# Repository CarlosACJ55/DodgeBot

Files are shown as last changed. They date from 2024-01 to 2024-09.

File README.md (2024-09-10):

# DodgeBot

<!-- [![Python application](https://github.com/CarlosACJ55/DodgeBot/actions/workflows/python-app.yml/badge.svg)](https://github.com/CarlosACJ55/DodgeBot/actions/workflows/python-app.yml) -->
## Youtube Demo Video Links
Dodgebot Purdue Boxing Club Review (https://youtube.com/watch?v=Q3NQfAVkUB4)

Dodgebot Demo 1 (https://www.youtube.com/shorts/NQUYcLnN8nE)
Dodgebot Demo 2 (https://youtube.com/shorts/Dirlxg9N7j0)

## Description

Punch-dodging robot project started as a senior design group project for ECE 47700 group 5 at Purdue University.

<!-- ### Project Website

Learn about PunchBot on our Project Website!
Https://engineering.purdue.edu/477grp5/ -->

### Dependencies

* Brains coded in Python 3
  - Packaged with **Poetry**
  - Developped with **Pytest**
  - Ui designed in **tkinter**
* Braum controlled by **STM32F7** programmed in **C**
  - Generated drivers with **STM32CubeMX**
  - Depelopped for **Yaskawa** **SGM7G-30A** & **SGM7G-20A** motors

## Authors

* Yusuf Jarada
* Maximillian Drach
* Ayman Motoda
* Carlos Cotera

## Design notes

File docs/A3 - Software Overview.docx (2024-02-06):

# Software Overview

# Year: 2024 Semester: Fall Team: 5 Project: PunchBot

# Creation Date: 01/23/2024 Last Modified: January 27, 2024

# Author: Carlos Cotera Email: ccoteraj@purdue.edu

# 1.0 Software Overview

PunchBot has a couple main requirements for success. From the perspective of a user, here is how the interactions are expected to go, as well as a highlight of where the key software is implemented:

After turning on the device, the user should be able to stand in view of the cameras, within arm’s reach, then a second user should be able to initialize punch detection mode1. At this point, the cameras continually analyze the movement of the player’s gloves and once the start of a punch is detected by the tracking script, we can now trigger the trajectory prediction algorithm2. Here, after quickly estimating the general direction of the punch, the robot should be able to determine an optimal dodging direction. Then, the STM and jetson chips use UART via EtherCAT to give the motors SPI commands3. The first motor is responsible for orienting PunchBot circularly to face a direction, while the second motor is meant to rapidly tilt the target forward to perform a dodge that imitates a real-life boxer by pivoting at an approximation of the hips.

At this point, the punch is completed and the bot will have to re-calculate how to return to its starting point as fast as possible, during the return, we expect that it would be best to continue in punch detection mode, so the bot is ready to interrupt itself and make another dodge, but this might prove to be either unnecessary given the final speed or too complex for the hardware, so we can still determine this later. Once back in punch detection mode we want the main script to cycle between these modes efficiently until the bot is deactivated via user input.

As a potential advancement, we could complete a game design for the project as described in the flowchart in the appendix 1 below, the main machine state functionality that we need to achieve is in appendix 2.

2.0 Description of Algorithms

Utilizing the OpenCV library, NumPy, and PyTorch for computer vision. The real-time video processing from a camera feed is done as follows, following the KMeans clustering approach to analyze motion via the kmeans PyTorch import:

Initializing

frame_resize: Resizes a video frame.

calibration_circle: Adds a calibration circle to the frame.

K-Means Clustering Functions:

kmeans_gpu: Applies K-Means clustering to identify objects in the video feed and returns their coordinates and cluster centers.

Initialize parameters like pixel center, camera height, user height, and camera orientation.

Main Loop:

Continuously captures video frames, converting frames to the HSV color space and applying color filtering to identify objects in the specified color range (yellow gloves). With this processed data, we use K-Means clustering to identify the objects' pixel coordinates and cluster centers. We can also track the movement of the identified objects and calculate avoidance maneuvers for a simulated robot.

# 3.0 Description of Data Structures

# Based on our mode functions, there would also be a need of data structures for motion tracking and motion analyzing. One of the key data structures we are taking advantage of for the PunchBot is a displacement vector for the following uses (examples from current testing script):

img_2_vector and vector_2_image: Convert image to vector and vice versa.

pixel_2_cords and cords_2_pixel: Convert pixel coordinates to real-world coordinates and vice versa.

To track the motion of user, we would need to set data points from the image of the user using camera. Inside this data structure, it will capture and tracks each data points of the user’s glove motion. By comparing x, y, z values, we can detect the punch because user will move their arms forward. In analyzing motion structure, it will calculate possible pathway of the punch based on the data point. I the main loop, punch detection mode captures frames from the camera, processes them, performs color segmentation, and tracks objects using k-means clustering. The tracked object's position and movement are used for some form of robotic control or object avoidance.

Examples of other key data structures:

lower_bound_gloves = np.array([20, 100, 100])

upper_bound_gloves = np.array([30, 255, 255])

color_mask_gloves = cv.inRange(hsv_frame, lower_bound_gloves, upper_bound_gloves)

Above, we use np arrays to produce a data structure that can perform vector like operations efficiently and with short, readable syntax. As for object Tracking with k-means:

marked_pixel_coords = np.column_stack(np.where(color_mask_gloves > 0)) marked_pixel_coords = torch.tensor(marked_pixel_coords, dtype=torch.float16, device=device) cord_list, punch_pixel_cord_centers = kmeans_gpu(marked_pixel_coords, 2, punch_pixel_cord_centers, num_punches)

This extracts coordinates of colored pixels and performs k-means clustering to identify objects.

The tracked object's centroids are calculated and used for further analysis.

# 4.0 Sources Cited:

E. Ecosystem, “Understanding K-Means clustering in machine learning,” Medium, May 17, 2022. [Online]. Available: https://towardsdatascience.com/understanding-k-means-clustering-in-machine-learning-6a6e67336aa1

# Appendix 1: Program Flowcharts (camera test)

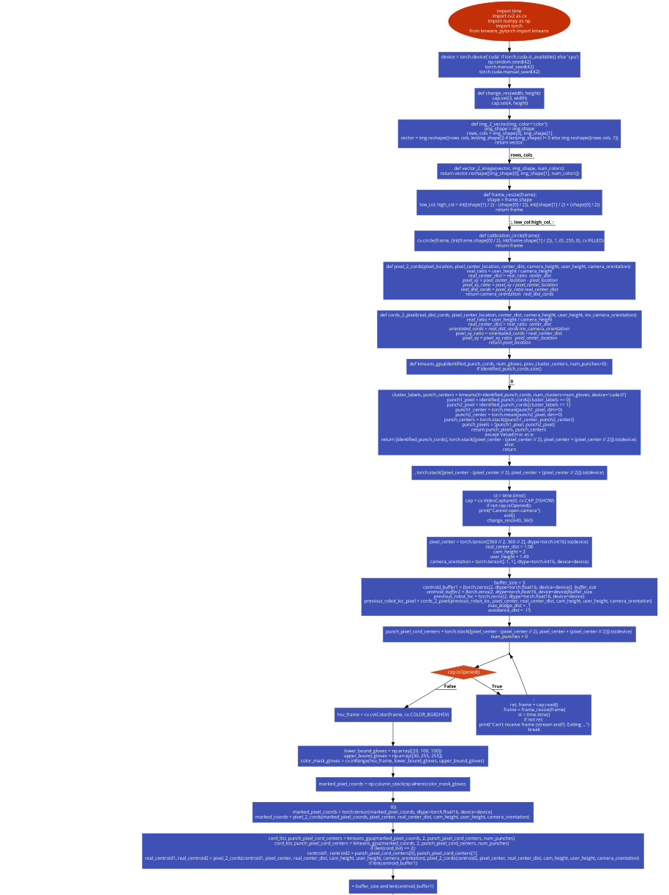
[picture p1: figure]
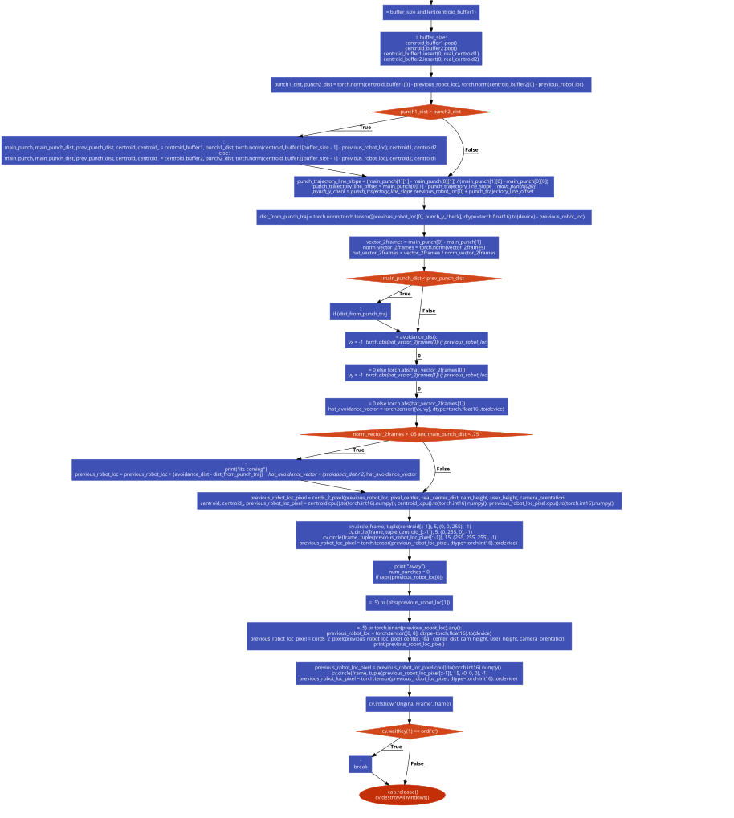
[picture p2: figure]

# Appendix 2: State Machine Diagrams

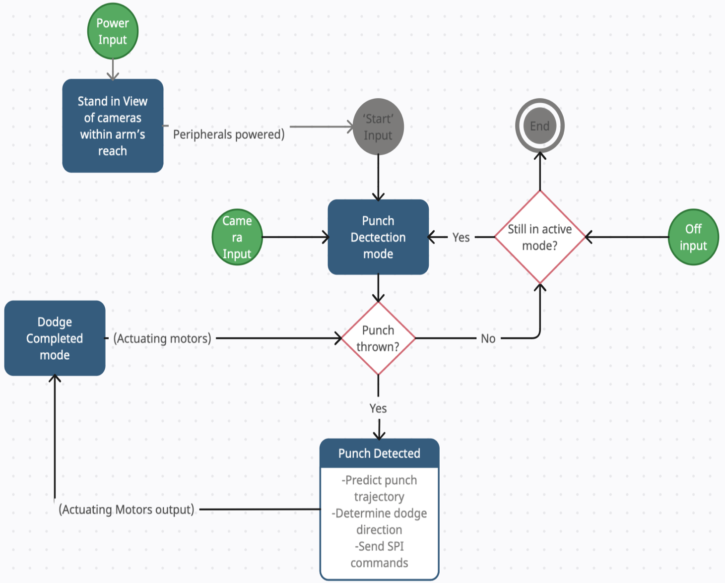
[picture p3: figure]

ECE 477: Digital Systems Senior Design Last Modified: 01-27-2024

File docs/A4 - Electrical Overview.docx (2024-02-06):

# Electrical Overview

# Year: 2024 Semester: Spring Team: 05 Project: Dodgebot

# Creation Date: February 1, 2024 Last Modified: February 1, 2024

# Author: Ayman Motoda Email: aelnamr@purdue.edu

# Assignment Evaluation: See Rubric on Brightspace Assignment

# 1.0 Electrical Overview

For this project, we are using a 32-bit microcontroller to communicate with an external computer to receive motor coordinates from the position calculation performed. We then take this value and feed it to the motor controller. To communicate with the computer, we are going to use UART at the maximum settable baud rate by the setup software to allow low latency between the controller and the computer. To communicate with the motor, we are going to use CANbus since this is the only natively supported communication protocol used by the microcontroller. The maximum baud rate of the motor interface is 1Mbit/s [1], so we are going to communicate with the motor at that rate also for lower latency.

# 2.0 Electrical Considerations

For our power delivery system, our input voltage is going to be at 12V and can be delivered at 5A. The required voltages for the different components around our board are going to be 5V and 3.3V. We will be using buck controllers to create these voltages. The STM32F2 chip that we are using has a typical operating voltage of 3.3V [2]. The NVIDIA Jetson computer that we are using has an operating voltage of 5V [3]. Any peripherals that are connected to both of these computers will be powered off by either of these chips.

The main essence of the operation of our robot is going to be speed. Our target is to dodge a punch that would occur in 100ms. We are going to allocate around 50ms to the computation and signal communication time. This means that having a higher clock speed will help in our baud rate in our communication systems. The maximum baud rate of UART on our STM32 chip is around 1Mbit/s [2]. This requires a clock rate of 16MHz for just the UART lines. The other communication system of CANbus will require the same baud rate and clock speed to run it. This means that at least a operating frequency of >32MHz is required for our system. For reliable operation, we will want to run at a frequency of >100MHz.

The total power that can be supplied to the board through the 12V input is 60W. The total output power that can be supplied by the switching regulators is 5V at 5A or 25W, and 3.3V at 5A or 16.5W[4]. The total power output by the regulators is 41.5W. Since we are using switching regulators that are at least 82% efficient, we only have a total power usage of 51W which is within our input supply power demands.

Device | Max Current Draw [A] (5V) | Device | Max Current Draw [A] (3.3V)
NVIDIA Jetson [3] | 4 | STM32F2 [2] | 0.120

# Table 1: Electrical Max Current Component Requirements

# Any peripherals connected to these devices are within the power draw specifications provided as they are powered off these computers/microcontrollers, so no additional power draw should occur.

# 3.0 Interface Considerations

The two utilized interfaces in this project are UART and CANbus. UART is used for communicating with the main computer. The main computer has the motor commands we need to send to the motor controllers. The STM32 and the Jetson are going to be set up for UART so that we can transmit this data. We chose this methodology because the distance is going to be short between both controllers, so using a synchronous protocol was not a concern since it will require less lines as well as making it much easier to integrate with the Jetson. The baud rate is also very high, so we can get very low latency between both controllers. A 1Mbit baud rate allows transmission times of way below 1ms [2]. The second communication protocol that is being used is CANbus. This is because this is the only way we can communicate with the motor controllers. This has the same baud rate as UART, so there is no bottle neck for each other except for the speed of the microcontroller to take the data and create the new packet frame for the other communication interface [5]. The peripheral interface that we will focus on is USB, which is built into the Jetson, but it is to receive the camera feed.

# 4.0 Sources Cited:

[1] “CAN-Bus Interface connector X13/X14,” Kollmorgen.com, 2023. https://webhelp.kollmorgen.com/akd2g/english/Content/AKD2G-S%20Install/e/AKD2S_install_09_21_00_CANbus%20interface.htm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 (accessed Feb. 01, 2024).

[2] STMicroelectronics, “Arm®-based 32-bit MCU, 150 DMIPs, up to 1 MB Flash/128+4KB RAM, USB OTG HS/FS, Ethernet, 17 TIMs, 3 ADCs, 15 comm. interfaces and camer,” STMicroelectronics STM32F205xx STM32F207xx, Jul. 2020. https://www.st.com/resource/en/datasheet/stm32f207vg.pdf

[3] NVIDIA, “DATA SHEET NVIDIA Jetson Nano System-on-Module Maxwell GPU + ARM Cortex-A57 + 4GB LPDDR4 + 16GB eMMC,” NVIDIA Developer, 2014. https://developer.download.nvidia.com/assets/embedded/secure/jetson/Nano/docs/JetsonNano_DataSheet_DS09366001v1.1.pdf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 (accessed Jan. 20, 2024).

[4] Texas Instruments, “LM2678 LM2678 SIMPLE SWITCHER ® High Efficiency 5-A Step-Down Voltage Regulator,” 2000. Accessed: Feb. 01, 2024. [Online]. Available: https://www.ti.com/lit/ds/symlink/lm2678.pdf?ts=1706759876304&ref_url=https%253A%252F%252Fwww.google.com%252F

[5] Kollmorgen, “CAN-Bus Interface Connector X13/X14,” Kollmorgen.com, 2023. https://webhelp.kollmorgen.com/akd2g/english/Content/AKD2G-S%20Install/e/AKD2S_install_09_21_00_CANbus%20interface.htm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

# Appendix 1: System Block Diagram

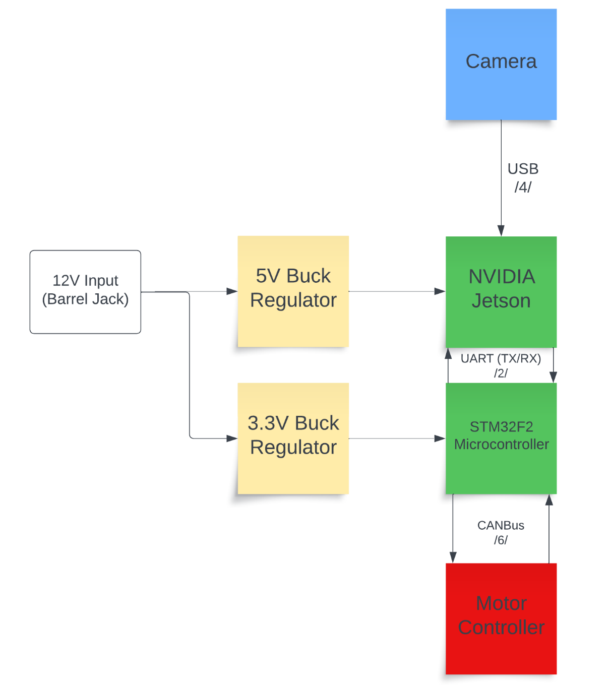
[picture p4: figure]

ECE 47700: Digital Systems Senior Design Last Modified: 09-04-2023

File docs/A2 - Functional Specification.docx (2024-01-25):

# Functional Specification

# Year: 2024 Semester: Spring Team: 05 Project: DodgeBot

# Creation Date: January, 2024 Last Modified: January 20, 2024

# Member1: Ayman Motoda Email: aelnamr@purdue.edu

# Member2: Maximilian Drach Email: mdrach@purdue.edu

# Member3: Yusuf Jarada Email: yjarada@purdue.edu

# Member4: Carlos Cotera Email: ccoteraj@purdue.edu

# Assignment Evaluation: See Rubric on Brightspace Assignment

# 1.0 Functional Description

PunchBot is designed to make physical training and reaction time improvement fun for children by simulating a dynamic environment where the robot responds to incoming punches. The device consists of a single punchable target mounted on an axle, allowing movement along a fixed base. The primary functionalities of the dodging robot are displayed in the functional block diagrams in appendices 2 & 3 but can be described as follows:

# Punch Detection:

# Utilizes a camera system to capture the surroundings in real time.

# Employs a color detection algorithm to identify brightly colored gloves worn by the user.

# Object Tracking:

# Implements an object detection and tracking algorithm to monitor the position and movement of the detected gloves continuously.

# Dodging Strategy:

# Executes a dodging strategy based on the tracked position of the gloves.

# Analyze and predict the trajectory of the gloves to enable the robot to move along the axle and avoid incoming punches.

# Motion Control:

Utilizes motors and an axle system for physical movement. Two motors and a differential allow the main axle to tilt forward as well as rotate itself in the same way a boxer would in real life. We will implement a control algorithm to ensure swift and accurate dodging movements based on real-time information from the camera system.

# 2.0 Theory of Operation

# Computer Vision System:

The computer vision system of the robot relies on a top-down birds-eye camera, which functions as the eyes of the robot by capturing real-time feed of the surrounding environment. This camera input is then processed by the computer vision system to detect and track the movement of objects, with a specific focus on monitoring the trajectory of incoming punches. The system's ability to analyze the visual data enables the robot to respond effectively to dynamic changes in its surroundings [4]. Look at Appendix 1.

Within the computer vision system, additional techniques have been employed for enhanced image processing. The system leverages the HSV color space and employs k-means clustering to segment the image effectively. This segmentation process enables the system to distinguish and identify pixels associated with the punch, particularly those corresponding to colored gloves. By utilizing the distinct properties of the HSV color space and the clustering capabilities of k-means, the computer vision system enhances its ability to accurately detect and isolate relevant elements in the image, contributing to the overall precision of punch detection [5,6].

# 3.0 Expected Usage Case

The Dodgebot project is designed to operate within indoor environments, requiring approximately 2 to 3 m² of clean space for optimal functionality. The system is configured to track punches and the robot uses a single camera, necessitating a controlled environment to ensure precise monitoring. Intended for a stationary setting, once the motors are set up and calibrated with the camera, the system remains in place. While players have the flexibility to move around the robot during interaction, the overall setup is expected to be stationary. Each instance of the project is tailored for a single user at a time in its prototype phase. The target user is ideally over 4 feet tall, with the primary requirement being the ability to throw a punch at the designated target. Minimal restrictions are placed on the user's nature, emphasizing physical capability over specific age or technical literacy considerations.

# 4.0 Design Constraints

# 4.1 Computational Constraints

The biggest computational constraint on this process will be the inverse kinematics equations required to move DodgeBot away from a punch. We will need to use object tracking to calculate the distance of the gloves relative to the head of the robot and determine how to move the robot to evade the attack most effectively. Our first attempt at object tracking will be a simple K-Means on marked gloves approach to tracking the position of everything. Next, we will have to establish certain rules on the system so that the robot can automatically evade punches, the distance from a punch must be greater than or equal to 5 inches for example. Finally, we will need to calculate the actual position of all the motors to move the robot to its desired position. This final calculation will be an inverse kinematics problem and will likely be the biggest bottleneck in terms of computational speed.

# 4.2 Electronics Constraints

The major external components of this project include a few key things. The ELP OV4689 camera is going to be the backbone of the operation of this robot, so it has a few parameters that limit our operation. The frame rate of the camera will decide how many frames we get in a certain time, so having a higher frame rate will increase how many points we can read before giving the decision algorithm its input data. Currently, the camera runs at a native 60FPS, so we may need to increase it if the algorithm does not get a valid input quickly enough. This interfaces through USB, but the Jetson already has this connection covered. The second main part external to the main computation system is the motor controller. Based on what motor controller we picked, we have a few options for communication, but currently, we will try to set up a connection over EtherCAT back to the STM32 which uses an ethernet port physically. This will require some special configuration since EtherCAT is not a natively supported interface in the STM manual. The last interface that we will need to set up is UART. This is to set up communication between the Jetson and the STM32 to send motor commands. This will not have a large challenge of impedance matching since the traces are going to be relatively short on our PCB.

# 4.3 Thermal/Power Constraints

Luckily, the power consumption of the computation and communication part of the electronics stack is going to be relatively low compared to the rest of the system. The Jetson draws a maximum of 4A at 5V, and the STM32 draws a maximum of 0.258A at 3.3V[1,2]. Since we will be using switching-based supply units of those voltages, the heat that is going to be dissipated is going to be relatively low. The Jetson also has a heatsink on board with the support of using a cooling fan and has a maximum temperature threshold of 97°C. The STM32 has a temperature threshold of 125°C [1,2]. Since the smaller peripherals are connected to power through one of these microcontrollers, their power usage is put together with them. The larger power constraint is going to come from the motors. The AKM2G motors that are being used have a supply voltage of 220V AC to the controller, and a single motor can draw a maximum of 37.6A [3]. We must ensure the circuits we plug the motor controllers into are rated for this current. Cooling is not a huge constraint since the movements we make are going to be so short, that the motors will not have enough time to heat up from these bursts of movement.

# 4.4 Mechanical Constraints

The device must be light enough to be carried around without extensive equipment. This may be unrealistic due to the size of the motors we are using. We also hope to keep all the electronics contained within the chassis of the device to preserve a clean aesthetic and safe design. Furthermore, regarding safety, the moving head joint must be fully constrained and secure to ensure that it does not move beyond its intended range. The head of DodgeBot is strong enough to be able to take a punch from a user and not break. This means that the device needs to be secured to the ground via weight or screws so it can handle that force, along with the force required to move the head of the robot fast enough to dodge punches. Finally, we want the project to last a long time with little maintenance so all mechanical components must be tested and rated for many uses.

# 4.5 Economic Constraints

This project has a $350 budget however the main cost comes from the price of the motors and motor controllers. We estimate this to be upwards of $8000. We contacted the school to pursue more funding and hope it will support us in this. Other than the motors, the rest of the components and materials are relatively cheap and do not pose any economic constraint on us.

# 4.6 Other Constraints

# 5.0 Sources Cited:

[1] STMicroelectronics, “STM32F765xx STM32F767xx STM32F768Ax STM32F769xx,” Aug. 2023. Accessed: Jan. 20, 2024. [Online]. Available: https://www.st.com/content/ccc/resource/technical/document/datasheet/group3/c5/37/9c/1d/a6/09/4e/1a/DM00273119/files/DM00273119.pdf/jcr:content/translations/en.DM002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

[2] NVIDIA, “DATA SHEET NVIDIA Jetson Nano System-on-Module Maxwell GPU + ARM Cortex-A57 + 4GB LPDDR4 + 16GB eMMC,” NVIDIA Developer, 2014. https://developer.download.nvidia.com/assets/embedded/secure/jetson/Nano/docs/JetsonNano_DataSheet_DS09366001v1.1.pdf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 (accessed Jan. 20, 2024).

[3] Kollmorgen Corporation, “Automation and Motion Control Programmable Automation Solutions,” Kollmorgen Products, 2021. https://www.kollmorgen.com/sites/default/files/AMC-KM_CA_000246_RevG_EN-mobile.pdf (accessed Jan. 20, 2024).

[4] Wikipedia contributors, “Angle of view (photography),” Wikipedia, Dec. 29, 2023. https://en.wikipedia.org/wiki/Angle_of_view_(photography)

[5] Wikipedia contributors, “HSL and HSV,” Wikipedia, Jan. 10, 2024. https://en.wikipedia.org/wiki/HSL_and_HSV

[6] Wikipedia contributors, “K-means clustering,” Nov. 20, 2023. https://en.wikipedia.org/wiki/K-means_clustering

‌

# Appendix 1: Camera Calibration Graph and Equation

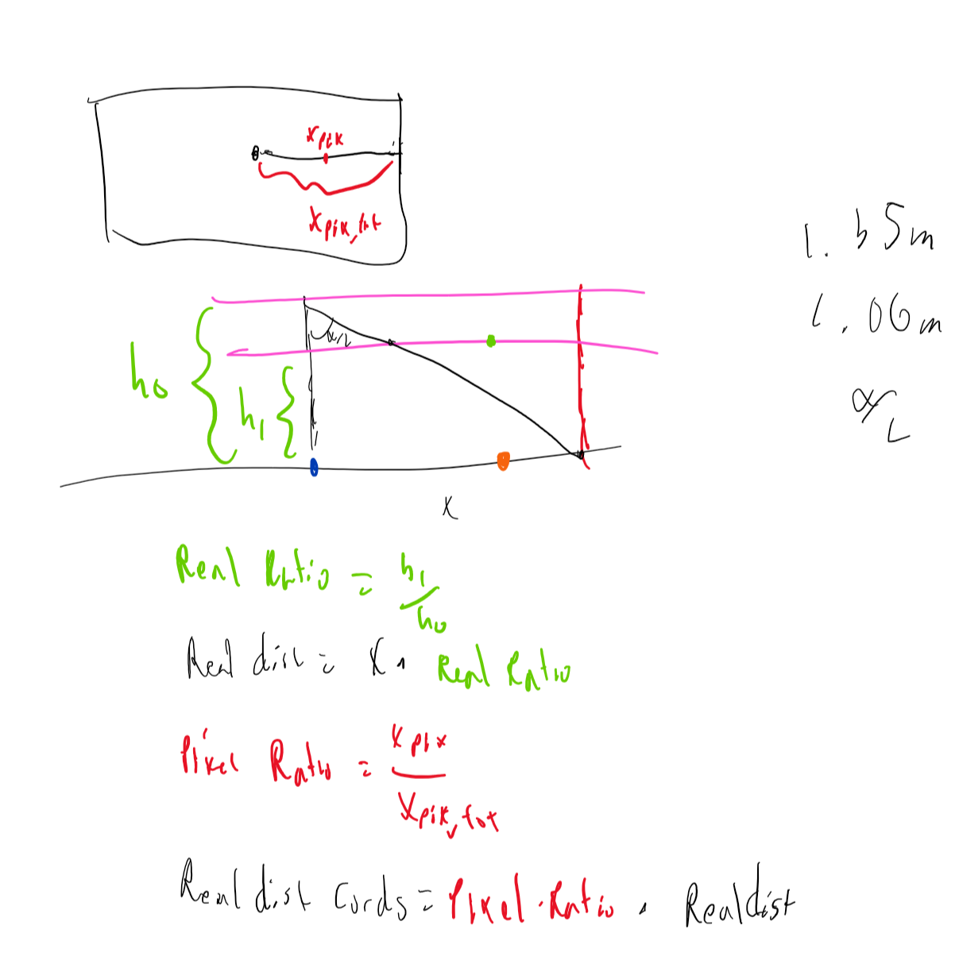
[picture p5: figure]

# Appendix 2: Functional Block Diagram

Top camera continuously feeding info to processor
Top and front camera data used to predict punch trajectory
Microcontroller controlls actuators
Motor 1 controls orientation of differential to aim punchbot's dodge
Motor 2 tilts forward to dodge as fast as possible
User punches
Punch start detected by embedded processor
Opposite motion resets to neutral position

# Appendix 3: Stretch Goals Function Block Diagram

# Accelerometer in target detects if punch was recieved Sound animation to confirm punch landed Or sound animation to taunt player if punch successfully dodged Game design creates more captivating interation with PunchBot Continuing from after a dodge is performed...

PBW – 23-Jan-2023 Page 2 of 3

ECE 47700: Digital Systems Senior Design Last Modified: 01/20/2024

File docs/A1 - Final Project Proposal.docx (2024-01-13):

Final Project Proposal

Year: 2024 Semester: Spring Team: 05 Project: Dodgebot

Creation Date: 01/09/2024 Last Modified: 01/09/2024

Team Members (#1 is Team Leader):

Member 1: Yusuf Jarada Email: yjarada@purdue.edu

Member 2: Maximillian Drach Email: mdrach@purdue.edu

Member 3: Carlos Cotera Email: ccoteraj@purdue.edu

Member 4: Ayman Motoda Email: aelnamr@purdue.edu

1.0 Project Description:

Hardware Components:

Robot Body:

- Design a simple and compact robot body that can move on an axle.
- Ensure that the design allows for easy bunching and dodging movements.

Axle and Motor System:

- Choose motors that can control the movement of the robot along the axle.
- Integrate an axle system that allows the robot to rotate and dodge punches.

Camera System:

- Select a camera with sufficient resolution and frame rate for real-time detection.
- Mount the camera in a way that provides a good field of view for detecting punches.

Color Detection System:

- Use sensors or image processing techniques to identify brightly colored gloves.
- Implement a system that can accurately distinguish the gloves from the background.

Microcontroller or Single-Board Computer:

- Choose a microcontroller or single-board computer (like Raspberry Pi or Arduino) to process camera input and control motors.
- Ensure it has the necessary processing power and interfaces for camera and motor control.

Software Components:

Image Processing Algorithm:

- Develop an image processing algorithm to analyze the camera feed.
- Identify and track the position of the brightly colored gloves in real-time.

Control Algorithm:

- Create a control algorithm that takes input from the image processing module.
- Implement a dodging strategy based on the detected glove positions.

Motor Control:

- Write code to control the motors based on the output from the control algorithm.
- Ensure the robot can move quickly and accurately to dodge punches.

Integration and Testing:

- Integrate the hardware and software components.
- Test the prototype in controlled environments to ensure accurate glove detection and effective dodging.

Refinement:

- Refine the algorithms and adjust parameters based on testing results.
- Fine-tune the robot's movements for better dodging performance.

Safety Measures:

- Implement safety features, such as emergency stop mechanisms, to ensure the safety of users and the robot itself.

Documentation:

- Document the design, code, and testing procedures for future reference or improvement.

2.0 & 2.1 & 2.2 & 2.1.1 Team Member Expertise and Team Roles and Responsibilities:

Team Member: Carlos Cotera – Software Lead

- Responsible for design and implementation of source code. Undertakes functional prototyping efforts early in the semester to mitigate risk in the later stages of the design process.

2.1.2 Team Member: Maximilian Drach – Systems Lead

- Responsible for high level functional overview of the system, including the theory of operation, block diagram, and component selection. Ensures components and systems on project work together coherently.

2.1.3 Team Member: Ayman Motoda – Hardware Lead

- Responsible for design of printed circuit board electrical schematics and layouts, often in charge of circuit board construction and packaging assembly

2.1.4 Team Member: Yusuf Jarada – Team Lead

- Maintains communication among team members, ensures team is progressing and assists fellow team members in addressing significant issues.

3.0 Homework Assignment Responsibilities

Design Component Report

A3-Software Overview: Carlos Cotera

A4-Electrical Overview: Ayman Motada

A6-Mechanical Overview: Yusuf Jarada

A8-Software Formalization: Maximilian Drach

Professional Component Report

A9-Legal Analysis: Maximilian Drach

A10-Reliability and Safety Analysis: Yusuf Jarada

A11-Ethical/Environmental Analysis: Carlos Cotera

A12-User Manual: Ayman Motada

4.0 Estimated Budget
1. Motors = $1,000
  a. The total is of a 3x quantity of 40Nm Hub Motors
2. Board, Micros = $210
  a. Requires a Jetson ($150) + STM32 ($30)
  b. Board + Components ($30)
3. ESC + Power Supply = $200
  a. DC-DC Converter & Inverter for Motor ($150)
  b. Components for supplying subcircuits at 5V, 3.3V ($50)
4. Mechanical Components = $100
  a. Ball and Socket Joint ($20)
  b. Shaft ($10)
  c. Belts ($50)
  d. Screws, Nuts, ETC. ($20)

5.0 Project Specific Design Requirements (PSDR)

Definitions:

- Punch - Strong enough force applied by a bare hand to create mild contusion on an average 21-year-old healthy male.
- Environment (Area) – The effective area in space, which the dodging system was design to monitor.
- System – The electrical makeup of the robot which involve the specified components.
1. An ability to track a punch and robot in the environment space.
2. An ability to create a set of coordinates that place the robots outside a punch trajectory path.
3. An ability to translate a set of coordinates into motor specific torque values to control the proper robot path.
4. An ability to supply a constant 5V and 3.3V to the microcontrollers and peripherals of the logic system at varying current demands.
5. An ability to communicate motor command data between both microcontrollers.

6.0 Sources Cited:

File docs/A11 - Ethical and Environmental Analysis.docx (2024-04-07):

# A11 - Ethical and Environmental Analysis

# Year: 2024 Semester: Fall Team: 5 Project: Dodgebot

# Creation Date: April 5, 2024 Last Modified: April 5, 2024

# Author: Carlos Cotera Email: ccoteraj@purdue.edu

# Assignment Evaluation: See the Rubric in the Brightspace Assignment

# 1.0 Environmental Impact Analysis

The manufacturing and end-of-life processes of the Robot Punch Dodging System may pose environmental concerns. While the components used are common in consumer electronics, certain manufacturing processes, such as PCB fabrication, involve potentially harmful chemicals. Additionally, the system's reliance on rare earth metals and non-biodegradable materials could contribute to environmental degradation during disposal. Diving deeper into the details:

# Manufacture

1. Chemical Usage: The manufacture of the Robot Punch Dodging System involves processes like PCB fabrication, which utilize hazardous chemicals. These chemicals pose risks to both human health and the environment due to their toxicity and potential for environmental contamination.
2. Material Selection: Rare earth metals and non-biodegradable materials are commonly used in electronic components, contributing to resource depletion, and increasing landfill waste.

# Normal Use

1. Energy Consumption: The system requires electricity, contributing to energy consumption and emissions.
2. Longevity: Short product lifespans can lead to increased electronic waste, as outdated or malfunctioning systems are disposed of prematurely.

# Disposal/Recycling:

1. Electronic Waste: Upon disposal, electronic components may release hazardous substances into the environment if not properly recycled or disposed of. Non-biodegradable materials contribute to landfill accumulation.
2. Rare Earth Metal Depletion: Disposal of electronic devices contributes to the depletion of rare earth metals, which are essential but limited in supply.

What is our team doing to address these Environmental Impact Concerns? Below are the specific considerations for each topic we have implemented to our process.

Manufacture

1. Chemical Management: By selecting reputable manufacturers to provide the core parts of DodgeBot: Motors - Yaskawa Microcontroller – STM32[1][2] We ensure that we can minimize the environmental impact in the early stages of the product manufacturing process. As you can read in the references above, the carbon footprint of an “Ultra-Low-Power” microcontroller unit and effective chemical waste management tactics make this a suitable option for managing our impact on pollution. The Yaskawa motors were also picked at a premium over other options, but the construction of the motors is much more solid which gives us leeway in case of malfunction from spilling any potentially hazardous substances.
2. Material Selection: We are also adhering to best practices when manufacturing the custom parts this project requires with the guidance of Purdue staff. This includes the mechanical casing for the motors made from aluminum and steel. The best part of these materials is that beside from being 100% reusable, at the amounts that we are using[³], the carbon footprint is very small. Given that the product is over 9000$ in materials cost alone, the carbon footprint impact per dollar cost of the final product will be minimized here.

# Normal Use

1. Energy Efficiency: Design the system for optimal energy efficiency, utilizing power-saving features and components to minimize energy consumption during normal use. By design, we will only be exerting the lease necessary power from the motors to move to the desired location, and we do not have any unnecessary features or animations besides safety protocols.
2. Longevity: Here, again we must come to mention the benefit of going with high-end motors. The durability of these machines will reduce the impact on the environment by reducing disposal. Furthermore, by using a general purposemicro controller and python based coed, it would be very easy to provide firmware updates and maintenance support to extend the useful life of the system.

Disposal/Recycling

1. Recycling Programs: Implement a comprehensive recycling program for electronic waste, allowing users to return outdated or non-functional systems for proper recycling and disposal of hazardous materials.
2. Material Recovery: Explore methods for recovering and reusing rare earth metals from discarded electronic components, reducing reliance on finite resources, and minimizing environmental impact.

By addressing environmental concerns at each stage of the product life cycle, including manufacture, normal use, and disposal/recycling, the Robot Punch Dodging System can minimize its environmental footprint and promote sustainability in electronic design and production. Through careful material selection, efficient manufacturing processes, and responsible end-of-life management, the system can mitigate environmental risks and contribute to a more sustainable future.

# 2.0 Ethical Challenges

The project raises ethical considerations regarding user safety and privacy when bringing the design to the market. Misuse of the system, such as attempting to interact with it while in motion, could lead to accidents or injuries. Proper warnings and precautions must be implemented to mitigate these risks. Additionally, the potential for electrical failures or data corruption emphasizes the need for clear user documentation and warnings. Lastly, avoiding misleading or deceptive advertising practices that could misrepresent the capabilities or limitations of the system will be key for the project to adhere to fair marketing practices. We have addressed these ethical challenges here:

# User Safety:

1. Testing and Validation: Our codebase is meticulously organized into classes, each serving a distinct purpose, to ensure clear separation of concerns and facilitate modular development. By aligning dependencies carefully, we isolate components for streamlined testing at every stage of the development cycle. Leveraging dependency injection enhances testability and flexibility by decoupling dependencies from the classes they serve, enabling deterministic and reproducible testing. Furthermore, we employ GitHub Actions for automated testing, integrating continuous integration and deployment pipelines into our workflow to provide transparent and reliable test results publicly. This approach not only ensures the stability and reliability of our firmware but also fosters accountability and transparency within our development process.
2. Warning Labels: Clearly label the system with warnings about potential risks and proper usage guidelines. Especially when it comes to the key areas of the circuit connection, given the high levels of power flowing through the motors. This includes placement of warning labels on the device itself and in user documentation.
3. User Education: Provide comprehensive user documentation that includes clear instructions on safe usage practices and potential risks associated with improper use. This can include guidelines for mounting the device securely and avoiding interaction while in motion. More importantly, it would be useful to implement a responsive questionnaire before the user can turn on the program. Users should be able to expect the behaviors of DodgeBot and be prepared as it operates.

# Privacy Concerns:

1. Data Security Measures: There is absolutely no data collected by the user that is shared over any sort of connection to any other parties and data collection is in no way a goal of this product.

Fair Marketing Practices:

1. Truthful Representation: Ensure that all marketing materials accurately represent the capabilities and limitations of the system. Avoid exaggerating performance or making unsubstantiated claims, especially to professional boxers, for whom this product might not be the best.

By addressing ethical challenges such as user safety, privacy concerns, and fair marketing practices, the team can ensure that the design and marketing of the Robot Punch Dodging System are conducted in an ethical and responsible manner. Through testing, transparent communication, and adherence to ethical principles, the team can build trust with users and potential stakeholders while promoting the ethical use of technology.

# 3.0 Sources Cited

[1] STMicroelectronics. (n.d.). Footprint of an Ultra-Low-Power MCU. [Online]. Available: https://www.st.com/content/st_com/en/about/st_approach_to_sustainability/sustainability-priorities/sustainable-technology/eco-design/footprint-of-an-ultra-low-power-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

[2] STMicroelectronics. (n.d.). Waste Management. [Online]. Available: https://sustainabilityreports.st.com/sr22/environment/waste.html

[3] 8 Billion Trees. (n.d.). Carbon Footprint of Steel. [Online]. Available: https://8billiontrees.com/carbon-offsets-credits/carbon-footprint-of-steel/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,1kg%20%3D%206.15CO2eq

https://engineering.purdue.edu/ece477 Page 1 of 2

ECE 47700: Digital Systems Senior Design Last Modified: 04-05-2024

ECE 477 Digital Systems Senior Design Project Rev 9/12

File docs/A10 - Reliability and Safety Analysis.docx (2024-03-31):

# A10 - Reliability and Safety Analysis

# Year: 2024 Semester: Spring Team: 5 Project: Dodgebot

# Creation Date: March 30, 2024 Last Modified: March 30, 2024

# Author: Ayman Motoda Email: aelnamr@purdue.edu

# 1.0 Reliability Analysis

The STM32F207VGT6 [1] is the main microcontroller onboard that is used to interface with the motor controllers, and the main computation system making it a very critical component of this system. Because of its very high complexity, and its relatively higher operating temperature compared to most components on the board, it was selected for this analysis.

The model used to find the failure rate of the STM32F2 chip is referred to as a microcircuit in the MIL-HDBK-217f [2] handbook since the Cortex M3 chip has more than 60k gates [3]. The environment this system is in is relatively controlled and isolated, so not a lot of environmental factors play a huge role in its failure rate. Most of the failure points come from its inherent design and manufacturing scheme, which is not in our control, but we can always add redundancy if the insane number of hours needed to fail the chip was reached.

# = λ_(BD) · π_(MFG) *π_T *π_(CD) + λ_(BP) · π_E · π_Q + λ_(EOS)

The TLV1117LV LDO [4] is a relatively simple chip, but it will also produce the most heat on the board, so it also has a higher chance of failing due to heat stress compared to most of the other components on the board. It is also critical for the operation of a lot of microchips on board, so its operation is vital to safe operation. This is classified as a linear microcircuit in the MIL-HDBK-217f [2] handbook, and has a relatively low transistor count, so most of the failure rate is going to be determined by its operating temperatures and its manufacturing tolerances.

# =(C_1 · π_T +C_2 *π_E ) · π_L · π_Q

The LM2678 Buck controller is also a relatively simple chip, but it will also produce a decent mount of heat which is also the reason it has a giant pad on the back of the package to dissipate the heat that is produced by the transistor. It is the most critical component of this board because ALL the ICs on board are in some way powered from this chip. Many of the chips use 5V power as well as many chips use the 3.3V power which is sourced from the LDO which sources its power from this buck controller. This is classified as a linear microcircuit in the MIL-HDBK-217f [2] handbook, and has a relatively low transistor count, so most of the failure rate is going to be determined by its operating temperatures and its manufacturing tolerances in the same way as the LDO.

# Table 1: STM32F207VGT6 Analysis

Parameter name | Description | Value | Comments regarding choice of parameter value, especially if you had to make assumptions.
λ_(BD) | Die Base Failure Rate | 0.16 | Logic Chip
π_(MFG) | Manufacturing Process Correction Factor | 0.55 | QPL Chip
π_(CD) | Die Complexity Correction Factor | A = 1.96cm² [1] Xs = 0.80 πcd = 0.36 [3]
λ_(BP) | Package Base Failure Rate | .0039 | 100 Pins
π_E | Environment Factor | 0.50 | Nonmobile, controlled environment use.
π_Q | Quality Factors | 10 | Commercial Part
λ_(EOS) | Electrical Overstress Failure Rate | .065 | Limited to 1000V [1]
Entire design:
λ_P | Failures per million Hours Rate | 0.11618
MTTF | Mean Time to Failure | 8607333.4

# Table 2: TLV1117LV Analysis

Parameter name | Description | Value | Comments regarding choice of parameter value, especially if you had to make assumptions.
C1 | Die Base Failure Rate | 0.2 | Linear Bipolar Chip
π_T | Manufacturing Process Correction Factor | 5.8 | Can reach a temperature junction of 150C in operation
C2 | Die Complexity Correction Factor | 0.0013 | 4 Pin Device
π_E | Environment Factor | 0.50 | Nonmobile, controlled environment use.
π_Q | Quality Factors | 10 | Commercial Part
π_L | Learning Factor | 1 | In production for more than a decade.
Entire design:
λ_P | Failures per million Hours Rate | 11.6065
MTTF | Mean Time to Failure | 86158.6

# Table 3: LM2678 Analysis

Parameter name | Description | Value | Comments regarding choice of parameter value, especially if you had to make assumptions.
C1 | Die Base Failure Rate | 0.2 | Linear Bipolar Chip
π_T | Manufacturing Process Correction Factor | 5.8 | Can reach a temperature junction of 125C in operation
C2 | Die Complexity Correction Factor | 0.0026 | 8 Pin Device
π_E | Environment Factor | 0.50 | Nonmobile, controlled environment use.
π_Q | Quality Factors | 10 | Commercial Part
π_L | Learning Factor | 1 | In production for more than 20 years.
Entire design:
λ_P | Failures per million Hours Rate | 11.613
MTTF | Mean Time to Failure | 86110.4

# Many of the components for the system are commercial parts which are fit for our application, but if we want to increase the rating on things like the power regulation circuits, we will need to purchase ICs that are rated for military operation.

# 2.0 Failure Mode, Effects, and Criticality Analysis (FMECA)

The criticality of this project realistically for all the MAIN components shown here are high or low. This is because many failure of the components that are displayed in the index below can result in catastrophic loss of control of the robot which can cause extremely violent mechanical results that could fatally injure or kill someone. All electrical failures that occur on the board will also be enclosed, so the risk is not very high if components fail catastrophically for the user since it is also very far away. The only low criticality is related to power loss since a loss of power guarantees that the operation of the robot halts. Since our risks are very high for this project, our failure rate for a high level is 10⁻¹⁰. For any of the low level failures, the acceptable failure rate is 10⁻⁶. Everything shown in the appendix from the schematic is necessary for necessary operation of the robot, so not every subcircuit was shown since they are not required or effect the operation of the robot. Many of the control schemes are redundant, and some of them give extra operations in case our demands change.

# 3.0 Sources Cited:

[1] STMicroelectronics, “STM32F205xx STM32F207xx,” Jul. 2020. Accessed: Mar. 31, 2024. [Online]. Available: https://engineering.purdue.edu/477grp5/Files/refs/stm32f207vg.pdf

[2] “Military Handbook Reliability Prediction of Electronic Equipment” Department of Defense. Washington DC. MIL-HDBK-217F, Dec. 2, 1991.

[3] A. Mittal, “Which ARM Cortex-M Processor?,” www.vlsiip.com, 2020. http://www.vlsiip.com/soc/soc_0003.html#:~:text=ARM%20Cortex%20M3%20Gate%20Count (accessed Mar. 31, 2024).

[4] Texas Instruments, “TLV1117LV 1-A, Positive Fixed-Voltage, Low-Dropout Regulator,” Jan. 2023. Accessed: Mar. 31, 2024. [Online]. Available: https://engineering.purdue.edu/477grp5/Files/refs/tlv1117lv.pdf

[5] Texas Instruments, “LM2678 SIMPLE SWITCHER ® High Efficiency 5-A Step-Down Voltage Regulator,” Jan. 2023. Accessed: Mar. 31, 2024. [Online]. Available: https://engineering.purdue.edu/477grp5/Files/refs/lm2678.pdf

# Appendix A: Schematic Functional Blocks

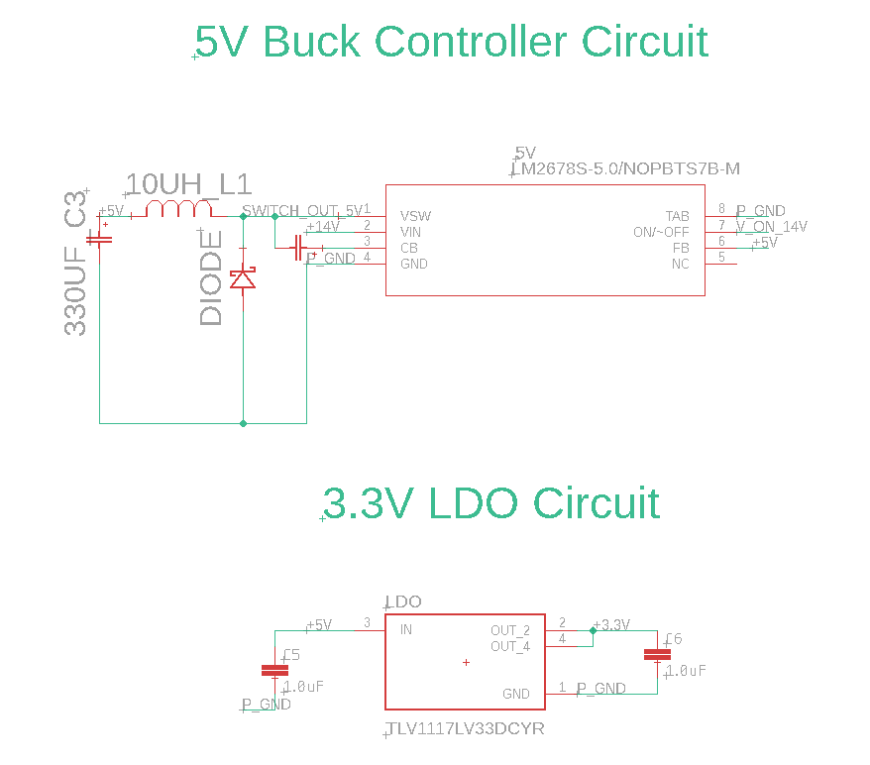
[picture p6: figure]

Figure 1: Power Topology

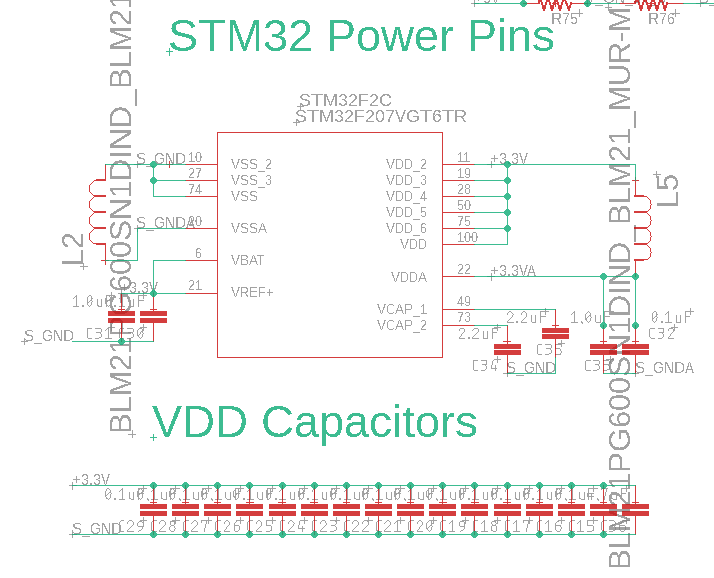
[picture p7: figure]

Figure 2: STM32 Power Supply Scheme

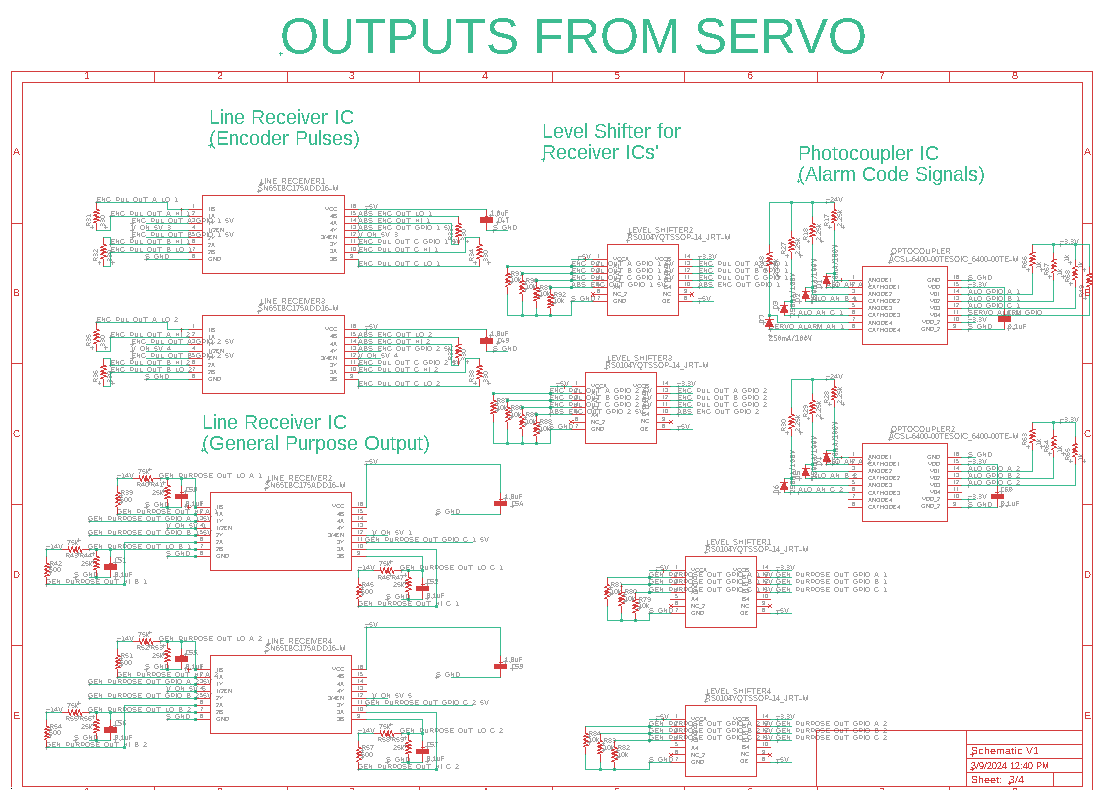
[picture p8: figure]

Figure 3: Servopack Output Topology

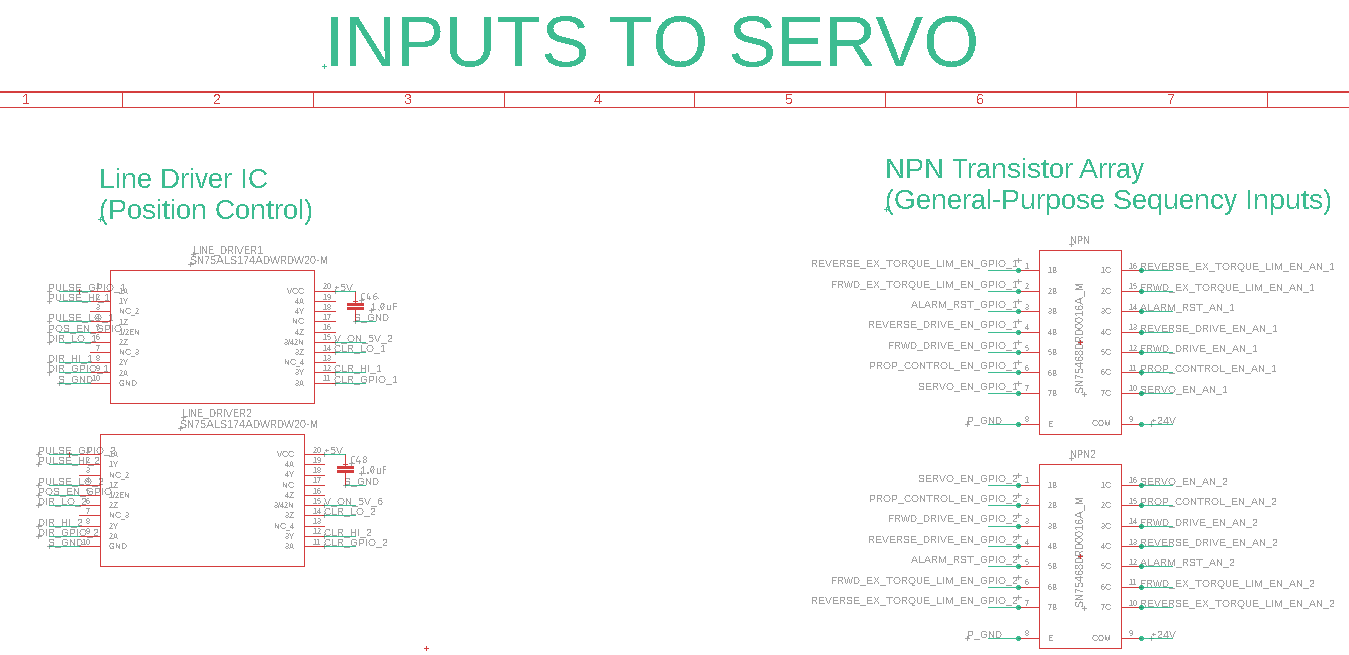
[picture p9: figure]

Figure 4: Inputs to Servopack Topology

# Appendix B: FMECA Worksheet

# Table 4: Power Topology & STM32 Power Topology FEMCA

Failure No. | Failure Mode | Possible Causes | Failure Effects | Method of Detection | Criticality | Remarks
1 | Voltage Drops on STM32 | C15-C29 | Can cause pulsations on outputs of pins which can cause extra pulse movements in motor commands | Encoder Feedback Count | High
2 | Voltage Loss | TLV1117LV & LM2678 | Shuts off the microcontrollers and ICs | Loss of robot operation, Power LEDs off. | Low | Robot will automatically stop moving at the loss of the enable signals and pulsations.
3 | High Voltage Fluctuation | LM2678 | Exceeds the maximum voltage output of the LDO which will burn it out which will kill power. | 3.3V LED Power detector off, maybe small amounts of smoke coming from the LDO IC | Low | With any of the main ICs off, the operation of the robot will be none since there are no control schemes that are operational. The box is also enclosed, so it is not a huge danger for the user if it occurs.

# Table 5: Outputs from Servopack FEMCA

Failure No. | Failure Mode | Possible Causes | Failure Effects | Method of Detection | Criticality | Remarks
3 | Line Receiver IC (Pulse Encoding) Signal Loss | SN65LBC175A Failure | Lose the ability to read the encoder, will throw off the positional reading to the computer which will cause movements that are unexpected. | Wild Movement, Large Delta between camera and motor position. | High
4 | Line Receiver IC (Pulse Encoding) Level Shifter Signal Loss | RS0104 Failure | Lose the ability to read the encoder, will throw off the positional reading to the computer which will cause movements that are unexpected. | Wild Movement, Large Delta between camera and motor position | High | Same result as the line-receiver IC, but with another point of failure since it’s also required to read the pulses.
5 | Photocoupler IC (Alarm Notification) Signal Loss | ASCL-6400 | Lose the ability to read the alarm code from the servo pack making diagnosis trickier. | Loss of robot movement without any apparent or obvious reason. | Low | Robot will shutoff when an alarm notification is sent, so even if we can’t read the notification, it is safe.

# Table 6: Power Topology & STM32 Power Topology FEMCA

Failure No. | Failure Mode | Possible Causes | Failure Effects | Method of Detection | Criticality | Remarks
6 | Line Driver IC (Pulse Transmission) Control Signal Loss | SN75ALS174 | Can cause pulse losses on the output side to the servo pack which can deviate the commands from the encoder which could throw off calculations | Encoder Feedback Count, Camera Detection Position and motor differential calculation. | High | Can eventually lead to robot drifting towards the edges of the operating range which can then collide with objects or other people around the robot.
7 | NPN Transistor Array Short | SN75468 | Lose the ability to turn off the control of the servopacks which could lead to unexpected motor movements based on microcontroller signals. | Random robot movements that are being sent even when the microcontroller shows that the enable signal is not being sent to the NPN array | High | Random movement of random amounts can eventually lead to exiting the operating range without any feedback system which can then collide with people and objects.

https://engineering.purdue.edu/ece477 Page 1 of 5

https://engineering.purdue.edu/ECE477 Page 1 of 5

ECE 477: Digital Systems Senior Design Last Modified: 10-20-2023

ECE 477 Digital Systems Senior Design Project Spring 2019

ECE 477 Digital Systems Senior Design Project Spring 2009

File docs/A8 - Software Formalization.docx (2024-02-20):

# Software Formalization

Year: 2024 Semester: Spring Team: 5 Project: Dodgebot

Creation Date: 02/15/24 Last Modified: 02/17/24

Author: Maximilian Drach Email: mdrach@purdue.edu (mdrach100@yahoo.com)

# 1.0 Utilization of Third-Party Software

Software | Description | Purpose | Licensing
STM32CubeIDE | A UI application for configuring STM microcontrollers. | Programming and testing GPIO pins via a user interface. | Free
AutoDesk | CAD design software | Designing motor enclosures for the robot. | Student license provided by Purdue.
Eagle | PCB design software | Designing PCB for communication and power systems. | Student license provided by Purdue.
VSCode | A free IDE for writing code. | Developing software components and algorithms. | Free

# 2.0 Description of Software Components

# The Dodgebot has 5 major components: user interface, image processing, object tracking, dodging algorithm, and motor control.

User Interface (UI):

- Development: Entirely built by our team using VS Code in Java.
- Platform: Runs on Dell XPS 9710 with an Intel I7-11800H and Nvidia RTX 3060 (60 W).
- Functionality: This interface handles displaying and collecting information for the user. The UI collects the users’ punch height (meters), the amount of time the user wants to play (minutes: seconds), and the start button which initiates the Dodgebot’s reaction system. The UI displays to the user the amount of time left to play before deactivating the Dodgebot’s reaction system and a non-emergency stop button.

Image Processing:

- Development: Entirely built by our team using VS Code in Python with NumPy and OpenCV libraries.
- Platform: Runs on Dell XPS 9710 with an Intel I7-11800H and Nvidia RTX 3060 (60 W). Processes data from an ELP-USBFHD08S-L29 camera over USB.
- Functionality: This program is responsible for the pre-processing of the original raw frame into a usable undistorted square frame. First, the distorted frame is sent over USB from the camera to the computer. Next, utilizing pre-derived empirical intrinsic and extrinsic weight matrices from Zhang’s calibration method [2] the frame is undistorted to an ideal pinhole camera frame. Finally, the frame is cropped into the center thus converting the 640x360 frame into 360x360 resolution.

Object Tracking:

- Development: Entirely built by our team using VS Code in Python with NumPy, Kmeans_pytorch, and OpenCV libraries.
- Platform: Runs on Dell XPS 9710 with an Intel I7-11800H and Nvidia RTX 3060 (60 W).
- Functionality: Responsible for utilizing the user input and processed image to track the real-space coordinate locations of the gloves (punches) and punch bag (Dodgebot). First, the pixels are converted to the HSV color space and then parsed to discern if any of the pixels match the color profile we are trying to track. The pixels that match the color profiles are then mapped to a real-space coordinate given the user’s input punch height using the P2C algorithm [1]. The real-space coordinates are then passed into either a punch or robot tracking processes that run in parallel.
  - The punch tracking utilizes K-Means to distinguish the two different punch coordinates and passes in the previous punch coordinate center to consistently track the same punch. The main punch that the robot is reacting to is deciding by comparing the L2 distance between the cluster centers and the robot center. The cluster with the smaller distance is considered the “main punch” which is then passed to the Dodging Algorithm.
  - The robot tracking averages the collection of points to find the point center. It then approximates the height of the robot using the location using the DP2C algorithm [1] and finally converts the pixel location to the real-coordinate location using the P2C algorithm [1].

Dodging Algorithm:

- Development: Entirely built by our team using VS Code in Python with NumPy library.
- Platform: Runs on Dell XPS 9710 with an Intel I7-11800H and Nvidia RTX 3060 (60 W).
- Functionality: Responsible for deciding the ideal location to dodge an incoming punch. Utilizes the Perpendicular Dodging Algorithm (PDA) [1] to determine Dodgebot's dodging direction.

Motor Control:

- Development: Entirely built by our team using VS Code in C and flashed onto the STM32F207VG.
- Platform: STM32F207VG microcontroller configured using STM32CubeIDE.
- Functionality: Receives rotational angle data via USB-UART. Converts and normalizes angle difference for proportional pulse position modulation. Controls Dodgebot's motor movements with the pulse width modulation.

# 3.0 Testing Plan

# User Interface:

- Priority: 3 (Medium)
- Test the UI systems by outputting the user input to the terminal and checking to see if the output values match the input given to the UI system.
- Also, check to see if the non-emergency stops button and the end of the timer outputs an interrupt to the terminal.

# Image Processing:

- Priority: 2 (High)
- Test if the system undistorts a checkerboard at the full resolution (640x360) by seeing if the checkboard looks like it was taken with a flat frame pin-hole camera. The reprojection error should be less than 1cm, which is the standard parameter error we are aiming for.
- Test the square algorithm by seeing if a center square is in the same location within the center of the frame when the resolution is changed from a full frame to 360x360.

# Object Tracking:

- Priority: 1 (Critical)
- Test our punch tracking systems by pre-measuring two real coordinate punch locations and comparing the output simulated real locations from the punch tracking algorithm.
- Will also track the system’s recognition of the incoming “main punch” by throwing punches at the expected target location and seeing which hand the computer associates with the “main punch”.
- Involves 20 consecutive testing trials in locations all over the tracking space, with at least 12 trials near the edge of the frame where distortion is the highest.
  - The simulated punch start location should be within 1cm of the measure start location.
  - We will track the system’s recognition of the incoming “main punch” by throwing punches at the expected robot location and seeing which hand the computer associates with the “main punch” (marked with a red circle).
  - If the start location is within 1cm tolerance and the “main punch” is always marked with a red circle throughout the duration of the jab, then this is considered a passing trial.
- Will test out robot tracking by pre-measuring the robot's z-coordinate space height and comparing the simulated z-coordinate height from the DP2C algorithm [1]. The threshold is 5% of the radius length of the robot’s height. If the z-simulated height is within the threshold of the real z-coordinate height, then it passes the test.

# Motor Control:

- Priority: 1 (Critical)
- Analog Testing:
  - Involves passing a simulated motor control angle to the microcontroller from the computer over a USB-UART interface, testing the output from the GPIO control pins on an oscilloscope, and measuring the difference between the expected pulse width and the output pulse width from the microcontroller.
  - The next step is to measure the signal delay between when new rotational angles are sent from the computer to when the pulse width modulations appear on the oscilloscope.
  - Measure the signal delay between the motor driver's rotational position data and the Dell XPS 9710 updated angles.
- Physical Testing:
  - After analog testing, use protractors to measure the initial angles on the robot arm and input a test rotational angle. Next, compare the new robot rotational angle with the expected results from the input angle change.

# Dodging Algorithm:

- Priority: 1 (Critical)
- Virtual Testing:
  - Outputs a captured frame with a circle to represent the simulated robot on the Dell XPS 9710. Track the circle’s movement around the frame to show where its simulated location would be given an input punch.
  - While this testing can test the general effectiveness, it is limited to the small frame size (360x360) and a delayed 60Hz display.
- Physical Testing:
  - Involves the entire Dodgebot pipeline and tests the effectiveness of the dodging algorithm in the real world. This testing can only be implemented after all the systems have passed their system test and the robot is safe to operate around.

# 4.0 Sources Cited:

[1] M. Drach, “Maximilian Drach ECE477 Journal Report,” https://engineering.purdue.edu/477grp5/. https://engineering.purdue.edu/477grp5/Team/progress/progress3.html (accessed Feb. 15, 2024).

[2] Z. Zhang, “A flexible new technique for camera calibration,” IEEE Journals & Magazine | IEEE Xplore, Nov. 01, 2000. https://ieeexplore.ieee.org/document/888718

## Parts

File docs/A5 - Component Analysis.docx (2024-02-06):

# Component Analysis

# Year: 2024 Semester: Spring Team: 05 Project: Dodgebot

# Creation Date: 02/01/2024 Last Modified: February 3, 2024

# Member 1: Yusuf Jarada Email: yjarada@purdue.edu

# Member 2: Ayman Motoda Email: aelnamr@purdue.edu

# Member 3: Maximillian Drach Email: mdrach@purdue.edu

# Member 4: Carlos Cotera Email: ccoteraj@purdue.edu

# 1.0 Component Analysis:

The major components we will cover will be crucial components of operation. The motors and drivers are a vital part to how responsive the robot is, and the motor drivers are a vital part in how complicated the motor controls will be to create. The camera is the second vital part of the robot since it determines how much information about the punches we get in the period that we set. The last one is about the microcontroller that we select since it will be responsible for the motor controls as well as the communication via UART to the main computer.

# 1.1 Analysis of Component 1:

Embedded sensors such as accelerometers and gyroscopes offer direct capture of motion data, facilitating precise tracking of movements. This movement data is highly accurate and monitors critical data about the direction of the punch. However, offloading sensor data to a remote computer has two non-ideal options: using a Bluetooth transmitter or data over wired cables. Bluetooth has a lower minimum latency of 20~30ms which is too slow of a time frame for a punch which reaches full extension at 100ms. [6] Sending the data over a cable introduces an extra cost to the user mobility experience when interacting with the Dodgebot (i.e. getting the way of the punch and dragging around).

Using a top-down camera allows us to use a faster frame rate of data that has lower latency. A MIPI-CSI2 Camera offers faster and high-resolution data transfer, but it can only send data for around 30 cm without signal degradation. [5] This means we would have to make sure the camera is close to the computer that is doing the image processing.

A USB 2.0 top-down camera presents a superior option for motion tracking compared to utilizing embedded sensors transmitting data over Bluetooth. With a frame rate of 260 fps, the camera ensures swift and precise tracking of movements. Its USB connection cable, boasting a latency of just 0.125 ms, facilitates rapid data transmission, resulting in faster updates and a continuous stream of high-quality frames. Additionally, the plug-and-play nature of USB cameras enhances ease of use and compatibility across various systems and platforms. Moreover, USB connections offer greater flexibility in terms of distance compared to MIPI-CSI2 interfaces, providing extended reach and versatility in deployment scenarios. These advantages underscore the efficiency of USB 2.0 top-down cameras for motion tracking applications.

Ultimately, we chose the USB 2.0 camera because of the ability to remotely interface with my more powerful component while still having low latency and easy to use for the end-user. We can easily plug and play with the camera over USB and don’t have to worry about where our processing unit is. This allows us to use my more powerful personal computer with a Nvidia 3060 instead of a Jetson Nano.

Component | Embedded Boxing Glove Sensor [7] | USB 2.0 Top-Down Camera [3] | MIPI-CSI2 Top-Down Camera [4]
Tracking Type | Accelerometer & Gyroscope | Camera Color Tracking | Camera Color Tracking
Communication Protocol | 2.4GHz Bluetooth v2.0 | USB 2.0 | MIPI-CSI2
Refresh Rate | ~30fps | ~260fps | ~206fps
Max Distance | >100m | >1m | ~30cm
Location | On Glove | Top-Down Bird’s Eye | Top-Down Bird’s Eye
Power Source | Battery | USB | MIPI
Cost | $166.50 | $68.30 | $15.00

# 1.2 Analysis of Component 2: Microcontroller

In the analysis of Component 2: Microcontroller, we evaluated two potential candidates, the STM32F207VG and the STM32F746ZG, for our DodgeBot project. Each microcontroller has its unique features, and the final choice is explained by the table below.

Criteria | STM32F207VG [1] | STM32F746ZG [2]
Clock Speed | Up to 120MHz | Up to 216MHz
RAM | 128kByte | 320kByte
Operating Voltage | 1.8 V to 3.6 V | 1.7 V to 3.6 V
Peak Current Consumption | 72mA (Run mode, full peripherals) | 235mA (Run mode, full peripherals)
UART IO Controllers | 3 (up to 10.5 Mbps) | 6 (up to 10.5 Mbps)
GPIO Pins | Up to 112 | Up to 168
Timers | Up to 17 timers – Up to twelve 16-bit and two 32-bit timers, up to 120 MHz, each with up to four IC/OC/PWM or pulse counter and quadrature (incremental) encoder input | Up to 18 timers: up to thirteen 16-bit (1x low- power 16-bit timer available in Stop mode) and two 32-bit timers, each with up to 4 IC/OC/PWM or pulse counter and quadrature (incremental) encoder input. All 15 timers running up to 216 MHz, 2x watchdogs, SysTick timer
Cost | $14.84 | $18.33

The STM32F207VG operates at a clock speed of up to 120MHz, which is only marginally lower than the STM32F746ZG. This microcontroller is also known for its lower power consumption compared to the STM32F746ZG. Although it has a slightly lower clock speed, the 100MHz required for the DodgeBot project is well within its capabilities. More importantly, the STM32F207VG may be more cost-effective, making it a suitable choice since we are already very tight on the budget at this stage of the project. Plus, while it may have fewer peripheral features compared to the STM32F746ZG, it offers sufficient capabilities for the Dodgebot project.

# Conclusion:

The STM32F207VG emerges as a suitable choice for our DodgeBot project due to its adequate clock speed for the project requirements, lower power consumption, and potentially lower cost. Since the DodgeBot project may not demand the extensive peripheral features of the STM32F746ZG, the STM32F207VG strikes a balance between performance and power efficiency. Things such as the improved M7 ARM as opposed to M3 are irrelevant to our project. As for peripheral features, the STM32F207VG meets both our needs of being UART compatible needs and has much more than the ~20 pins we will require to control DodgeBot. At the same time, the more extensive features on the STM32F746ZG are nothing that we might need.

# 1.3 Analysis of Motor + Drivers:

The motor drivers and motors themselves for the purposes of this project come as a package for the feasibility of interfacing the system with our microcontroller so that we do not need to have a motor control card on our end of the system. We had a few design constraints to the power requirements that we needed for the motors based on the dynamics that were tested (see Appendix A). To create these speeds, we need motors of the following specifications:

Specification | Value
Torque (X-Axis) | >= 28Nm
Torque (Y-Axis) | >= 40Nm
Weight (X-Axis) | <= 9kg
Voltage Supply | 110V – SP | 220V – SP | 220V – TP
Achievable Speed @ Torque | 600RPM

For our breakdown, there were two main lines of motor systems that we looked at. The Kollmorgen AKM2G line and the Yaskawa SGD7G line of motors were the only ones on the market that offered both the motor as well as the motor driver that had built in motor interface commands. The specifications for the motors are shown below:

# Motor:

Specification | AKM2G-53L [9] | SGM7G-30A [8] | SGM7G-20A [8]
Torque (X-Axis) | 40Nm | x | 28.7Nm
Torque (Y-Axis) | 40Nm | 54Nm | x
Weight (X-Axis) | 8.89kg | 13.5kg | 8.6kg
Motor Face Width | 114mm | 180mm | 130mm
Achievable Speed @ Torque | 748RPM | 2000RPM | 2600RPM
Peak Current Draw | 37.6A | 70A | 42A
Price | $2394 | TBD | TBD

# Driver:

Specification | AKD2G-SPC-6V12S [9] | SGD7W-330A00A [8]
Communication Interface | CANBus | Analog Input/Output
Voltage Supply | 220V – SP | 220V – TP | 220V – TP
Peak Current Delivery | 30A | 84A
Price | $2220 | TBD

Some main considerations for this project are the few differences there are between the motors and our application. The Kollmorgen motors do not need to be different from each other from each axis since their specifications were wide enough to fit both roles of the robot. The Yaskawa motors, however, required 2 different motors since the extra torque needed to meet the Y-Axis requirements resulted in over 5kg of added weight and 50mm of extra inertia that would need to be rotated. The resulting smaller motor has the torque needed, but it is also less than the Kollmorgen motor, but it is slightly lighter even though slightly bigger. With all these differences in specifications, the rotational dynamic data shows that either configuration will fit the performance characteristics needed for the robot to operate. One advantage to the Yaskawa motors is the speed characteristics. While we will probably never reach the speeds that the motors can operate it, it does give us additional options to gear down if we need to, based on the speed of the prototyped motor. The Kollmorgen motors do not have any room to gear since they are just barely above the rotational speed requirements. The biggest difference will be the current requirement for the motors and shows the biggest difference in technology. The Kollmorgen motors are based on a BLDC design which uses permanent magnets to operate. The Yaskawa motors are AC motors which require fewer complex controls to operate and are typically cheaper technology to produce, but they require much more power for the equivalent torque values. Even though the Yaskawa motors draw more current, both motors require 220V power whether it be single phase or three phase power to operate. The communication interface for the Kollmorgen motors is ran off CANBus which is a robust communication interface that doesn’t require any special circuitry to communication besides the connector between the microcontroller, and specifically placed resistors along the network. This does require more software involvement in sending motor commands as well as reception techniques of the microcontroller to read and send data quickly. The Yaskawa motors rely fully from analog signals which does require line drivers to send and receive signals, but they are much easier to diagnose, read, and create preconfigured commands to send to the motor controller from simple power electronics techniques. The final detail in the comparison is the price. The Kollmorgen motors totaled to over $10000 after options, which is a little over the proposed budget estimate that was given, but it was also kind of expected since the Kollmorgen controllers required specially made cables that cost $1000 on top off the extra few hundred dollars for each component (see Appendix B). While we have not received an official quote from Yaskawa for the motors and drivers, quick google searches online for similar products of specification put the motors and drivers in the $1500 range for each component which is significantly cheaper than the Kollmorgen option as well as the cable options are not custom, so they are expected to be cheaper too.

While the drawbacks of both are not detrimental to the performance of the robot, we have ended up trying to order the Yaskawa motors. For this course, the lead time for the motors and drivers is about 6 weeks which is too long for us to consider since we need to test the system before we are able to implement it. The Yaskawa motors also have a lead time that is within days which allows us more time to tweak the design to fit our needs. They also have control schemes that are much more easily programmable and do not require more complex software to operate.

# 2.0 Sources Cited:

[1] S. .com, “STM32F207VG,” STMicroelectronics, https://www.st.com/en/microcontrollers-microprocessors/stm32f207vg.html (accessed Feb. 3, 2024).

[2] S. .com, “STM32F746ZG,” STMicroelectronics, https://www.st.com/en/microcontrollers-microprocessors/stm32f746zg.html (accessed Feb. 3, 2024).

[3] “ELP 2.9mm lens 260fps USB Webcam Full HD 2MP CMOS OV4689 Sensor Mini 1080P 60fps Camera Board Module Wide Angle [ELP-USBFHD08S-L29] - $68.30 : ELP USB Webcam.” https://www.webcamerausb.com/elp-wide-angle-260fps-usb-webcam-2megapixels-cmos-ov4689-sensor-mini-1080p-60fps-camera-board-module-with-29mm-lens-p-269.html

[4] “Raspberry Pi Documentation - camera.” https://www.raspberrypi.com/documentation/accessories/camera.html

[5] “Design considerations for connecting analog devices video decoders to MIPI CSI-2 receivers.” https://www.analog.com/en/resources/app-notes/an-1337.html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,25%20cm%20to%2030%20cm.

[6] S. Harding, “What’s Bluetooth LE Audio? Explaining the spec and what it means for wireless sound,” Ars Technica, Jul. 12, 2022. https://arstechnica.com/gadgets/2022/07/whats-bluetooth-le-audio-explaining-the-latest-wireless-tech-standard/

[7] Yost Labs, “3-SpaceTM Bluetooth - Yost Labs,” Yost Labs. https://yostlabs.com/product/3-space-bluetooth/

[8] “SIGMA-7.” Accessed: Feb. 04, 2024. [Online]. Available: https://www.yaskawa.com/delegate/getAttachment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

‌[9] Kollmorgen, “AKM ® 2G Servo Motor Selection Guide with AKD ® Family Servo Drive Systems,” 2019. Available: https://www.kollmorgen.com/sites/default/files/AKM2G-KM_SG_000315_RevC_EN-mobile_ed.pdf

Appendix A: Motor Dynamics

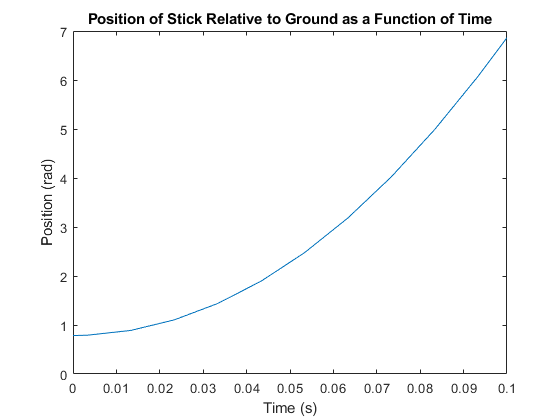
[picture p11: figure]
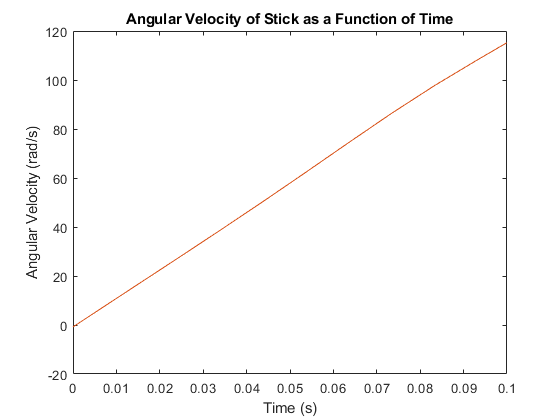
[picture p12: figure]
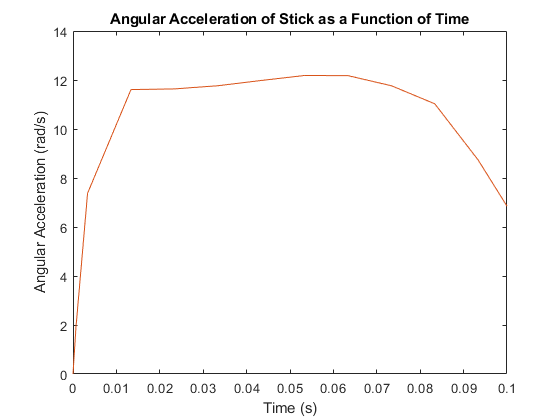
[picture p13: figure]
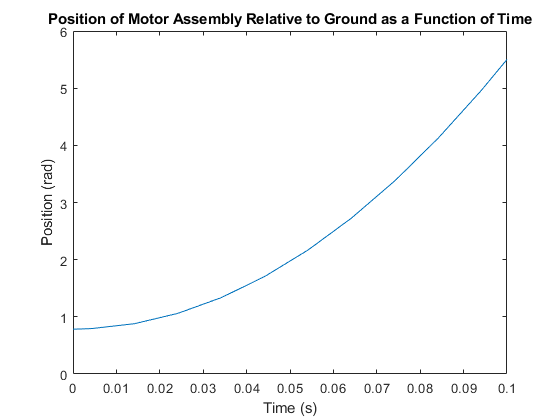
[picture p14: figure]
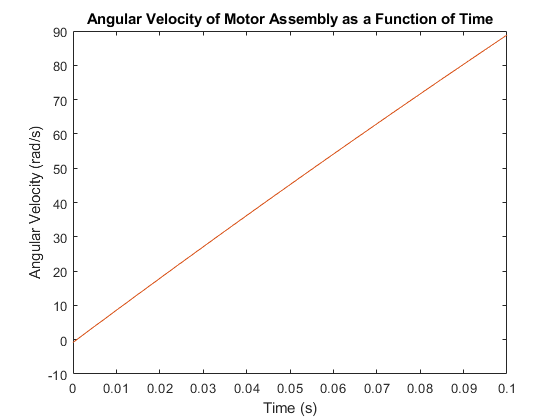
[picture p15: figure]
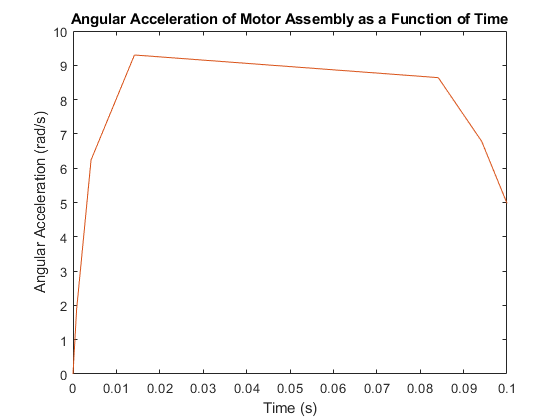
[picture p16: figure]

Appendix B: Kollmorgen Quote

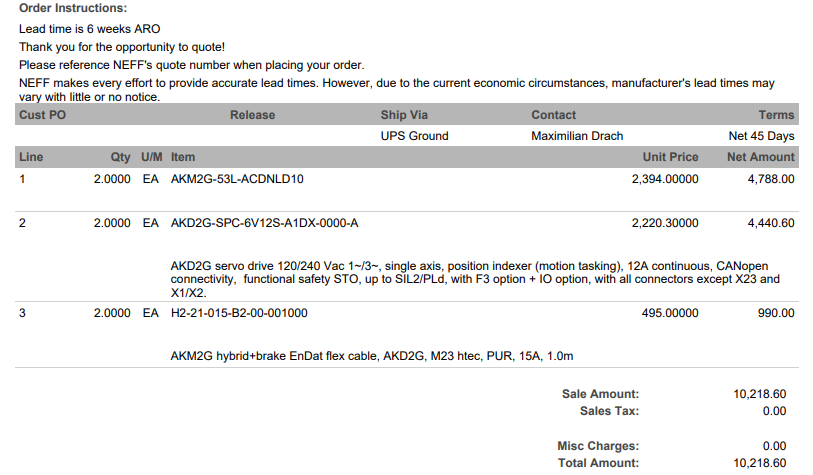
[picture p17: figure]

ECE 47700: Digital Systems Senior Design Last Modified: 09-07-2023

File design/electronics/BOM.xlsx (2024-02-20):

Part Number | Part Description | Quantity | Price | Total
STM32F207VGT6 | STM Chip | 1 | $14.84 | $14.84 |  | https://www.digikey.com/en/products/detail/stmicroelectronics/STM32F207VGT6TR/4357621
LM2678S-5.0/NOPB | 5V Buck Controller | 1 | $6.80 | $6.80 |  | https://www.digikey.com/en/products/detail/texas-instruments/LM2678S-5.0%2FNOPB/363825?gad_source=1
TLV1117LV33DCYR | 3.3V LDO | 1 | $0.35 | $0.35 |  | https://www.digikey.com/en/products/detail/texas-instruments/TLV1117LV33DCYR/2666508
20SVPF180M | 180 uF Cap | 1 | $1.39 | $1.39 |  | https://www.digikey.com/en/products/detail/panasonic-electronic-components/20SVPF180M/4204831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
CDBC520-HF | Buck Con. Diode | 1 | $0.61 | $0.61 |  | https://www.digikey.com/en/products/detail/comchip-technology/CDBC520-HF/5226193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
SRP1270-100M | 10uH Inductor | 1 | $1.55 | $1.55 |  | https://www.digikey.com/en/products/detail/bourns-inc/SRP1270-100M/2562126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
10SVPC330M | 330uF Cap | 1 | $1.86 | $1.86 |  | https://www.digikey.com/en/products/detail/panasonic-electronic-components/10SVPC330M/5719731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
GRM2195C1H103JA01D | 0.01uF Cap (0805) | 1 | $0.25 | $0.25 |  | https://www.digikey.com/en/products/detail/murata-electronics/GRM2195C1H103JA01D/586788
SN75ALS174ADWR | Line Driver IC | 2 | $3.35 | $6.70 |  | https://www.digikey.com/en/products/detail/texas-instruments/SN75ALS174ADWR/1593485
SN65LBC175AD | Line Receiver IC | 4 | $6.26 | $25.04 |  | https://www.digikey.com/en/products/detail/texas-instruments/SN65LBC175AD/380303
PJ-202AH | Barrel Jack Connector (24V) | 1 | $0.69 | $0.69 |  | https://www.digikey.com/en/products/detail/cui-devices/PJ-202AH/408450
PJ-025 | Barrel Jack Connector (14V) | 1 | $0.74 | $0.74 |  | https://www.digikey.com/en/products/detail/cui-devices/PJ-025/724801
OPA4205ADR | General Op-Amp (4 channel) | 1 | $6.42 | $6.42 |  | https://www.digikey.com/en/products/detail/texas-instruments/OPA4205APWR/17394950
LM43601PWPR | -15V Boost Inverter | 1 | $4.15 | $4.15 |  | https://www.digikey.com/en/products/detail/texas-instruments/LM43601PWPR/4965739
VLS201610CX-220M-1 | 22uH Inductor | 1 | $0.35 | $0.35 |  | https://www.digikey.com/en/products/detail/tdk-corporation/VLS201610CX-220M-1/5169796
UWD1V680MCL1GS | 68uF Capacitor | 1 | $0.53 | $0.53 |  | https://www.digikey.com/en/products/detail/nichicon/UWD1V680MCL1GS/3963027
3352T-1-203LF | 20k Potentiometer | 1 | $3.39 | $3.39 |  | https://www.digikey.com/en/products/detail/bourns-inc/3352T-1-203LF/1088346
SN75468DR | NPN Transistor Array | 2 | $0.86 | $1.72 |  | https://www.digikey.com/en/products/detail/texas-instruments/SN75468DR/2255090?gad_source=1
ACSL-6400-00TE | Optocoupler | 2 | $8.67 | $17.34 |  | https://www.digikey.com/en/products/detail/broadcom-limited/ACSL-6400-00TE/825239
1N4148WS-13-F | 1N4148 Diode | 6 | $0.21 | $1.26 |  | https://www.digikey.com/en/products/detail/diodes-incorporated/1N4148WS-13-F/4249326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
TST-105-01-F-D | STMLink Connector | 1 | $2.68 | $2.68 |  | https://www.digikey.com/en/products/detail/samtec-inc/TST-105-01-F-D/9497108
SSW-106-02-TM-S-RA | UART Connector | 1 | $1.20 | $1.20 |  | https://www.digikey.com/en/products/detail/samtec-inc/SSW-106-02-TM-S-RA/7891818
TL6330AF200Q | RST Button | 1 | $0.88 | $0.88 |  | https://www.digikey.com/en/products/detail/e-switch/TL6330AF200Q/8032037
BLM21PG600SN1D | Ferrite Bead | 3 | $0.12 | $0.36 |  | https://www.digikey.com/en/products/detail/murata-electronics/BLM21PG600SN1D/584263
5988191107F | Blue LED | 1 | $0.59 | $0.59 |  | https://www.digikey.com/en/products/detail/dialight/5988191107F/1291280
LTW-170TK | White LED | 1 | $0.61 | $0.61 |  | https://www.digikey.com/en/products/detail/liteon/LTW-170TK/758704
5988110107F | Red LED | 1 | $0.29 | $0.29 |  | https://www.digikey.com/en/products/detail/dialight/5988110107F/1291272
5988170107F | Green LED | 1 | $0.29 | $0.29 |  | https://www.digikey.com/en/products/detail/dialight/5988170107F/1291278
RS0104YQ | Level Shifter | 4 | $0.67 | $2.68 |  | https://www.digikey.com/en/products/detail/runic-technology/RS0104YQ/14544678
ERJ-P06J681V | 680 Ohm 1/2W Resistor | 1 | $0.13 | $0.13 |  | https://www.digikey.com/en/products/detail/panasonic-electronic-components/ERJ-P06J681V/525296
ERJ-P06J561V | 560 Ohm 1/2W Resistor | 1 | $0.13 | $0.13 |  | https://www.digikey.com/en/products/detail/panasonic-electronic-components/ERJ-P06J561V/525286
DD50P564GTXLF | 50 Pin Analog Connector | 2 | $5.82 | $11.64 |  | https://www.digikey.com/en/products/detail/amphenol-icc-(fci)/DD50P564GTXLF/4269156?gad_source=1
RMCF0805FT25K5 | 25.5k Resistor | 8 | $0.10 | $0.80 |  | https://www.digikey.com/en/products/detail/stackpole-electronics-inc/RMCF0805FT25K5/1712905
RMCF0805FT75K0 | 75k Resistor | 9 | $0.10 | $0.90 |  | https://www.digikey.com/en/products/detail/stackpole-electronics-inc/RMCF0805FT75K0/1760535
RMCF0805FT105K | 105k Resistor | 1 | $0.10 | $0.10 |  | https://www.digikey.com/en/products/detail/stackpole-electronics-inc/RMCF0805FT105K/1712620
CRCW080573K2FKEA | 73.2k Resistor | 5 | $0.10 | $0.50 |  | https://www.digikey.com/en/products/detail/vishay-dale/CRCW080573K2FKEA/1175850
RMCF0805FT1M00 | 1M Resistor | 1 | $0.10 | $0.10 |  | https://www.digikey.com/en/products/detail/stackpole-electronics-inc/RMCF0805FT1M00/1760080
RMCF0805FT88K7 | 88.7k Resistor | 1 | $0.10 | $0.10 |  | https://www.digikey.com/en/products/detail/stackpole-electronics-inc/RMCF0805FT88K7/1713411
RMCF0805FT10K0 | 10k Resistor | 5 | $0.10 | $0.50 |  | https://www.digikey.com/en/products/detail/stackpole-electronics-inc/RMCF0805FT10K0/1760676
RA73F2A2K26BTD | 2.25k Resistor (1W) | 6 | $1.33 | $7.98 |  | https://www.digikey.com/en/products/detail/te-connectivity-passive-product/RA73F2A2K26BTD/16031415
RMCF0805FT100R | 100 Resistor | 1 | $0.10 | $0.10 |  | https://www.digikey.com/en/products/detail/stackpole-electronics-inc/RMCF0805FT100R/1760711
RMCF0805FT75R0 | 75 Resistor | 1 | $0.10 | $0.10 |  | https://www.digikey.com/en/products/detail/stackpole-electronics-inc/RMCF0805FT75R0/1760492
RMCF0805FT330R | 330 Resistor | 8 | $0.10 | $0.80 |  | https://www.digikey.com/en/products/detail/stackpole-electronics-inc/RMCF0805FT330R/1760484
RMCF0805FT499R | 499 Resistor | 8 | $0.10 | $0.80 |  | https://www.digikey.com/en/products/detail/stackpole-electronics-inc/RMCF0805FT499R/1760282
RMCF0805FT1K00 | 1k Resistor | 6 | $0.10 | $0.60 |  | https://www.digikey.com/en/products/detail/stackpole-electronics-inc/RMCF0805FT1K00/1760090
CL21B104KCFNNNE | 0.1u Capacitor (X7R) | 29 | $0.03 | $0.78 |  | https://www.digikey.com/en/products/detail/samsung-electro-mechanics/CL21B104KCFNNNE/5961324
CL21C100CBANNNC | 10p Capacitor | 1 | $0.10 | $0.10 |  | https://www.digikey.com/en/products/detail/samsung-electro-mechanics/CL21C100CBANNNC/3888219
CL21B105KBFNNNE | 1u Capacitor | 10 | $0.07 | $0.75 |  | https://www.digikey.com/en/products/detail/samsung-electro-mechanics/CL21B105KBFNNNE/3886687
CL21A475KBQNNNE | 4.7u Capacitor (X7R) | 3 | $0.23 | $0.69 |  | https://www.digikey.com/en/products/detail/samsung-electro-mechanics/CL21A475KBQNNNE/3886906
CL21A225KB9LNNC | 2.2u Capacitor (X7R) | 3 | $0.27 | $0.81 |  | https://www.digikey.com/en/products/detail/samsung-electro-mechanics/CL21A225KB9LNNC/3888067
CL21B474KBFNNNE | 470n Capacitor (X7R) | 1 | $0.10 | $0.10 |  | https://www.digikey.com/en/products/detail/samsung-electro-mechanics/CL21B474KBFNNNE/3886697
CL21C121JDCNNNC | 120p Capacitor (X7R) | 1 | $0.10 | $0.10 |  | https://www.digikey.com/en/products/detail/samsung-electro-mechanics/CL21C121JDCNNNC/3886859
CL21A106KAYNNNE | 10u Capacitor (X7R) | 1 | $0.18 | $0.18 |  | https://www.digikey.com/en/products/detail/samsung-electro-mechanics/CL21A106KAYNNNE/3888549
 |  |  |  | Final Total: | $134.35
 |  |  |  | What we have to pay: | $98.73

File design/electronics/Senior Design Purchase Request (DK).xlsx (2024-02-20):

College of Engineering Senior Design Purchase Request Form |  |  | Department Name: | Today's Date: | 2024-02-13
 |  |  | ECE | Need-By Date: | ASAP
Vendor: | Digikey |  | Team Name / Project: | Your Name: | Ayman Motoda |  |  | <-- Put your name and also your team number in the Your Name: box
Website: | https://www.digikey.com/ |  | ECE 47700 / Team 05 | Building Abbv.: | BHEE
Phone Number: | 1-800-344-4539 |  |  | Room Number: | 007
Vendor Contact: |  |  | Account Number: | Phone Number: | 2405135229 |  |  | <-- Your Phone number
Contact Email: | sales@digikey.com |  | 7600000796 | Email Address: | aelnamr@purdue.edu |  |  | <-- Your PURDUE email
ITEM NAME / PART NUMBER |  | DESCRIPTION & LINK |  |  | QUANTITY | UNIT COST | TOTAL COST
497-18998-1-ND |  | STM Chip |  |  | 2.00 | $14.84 | $29.68
LM2678S-5.0/NOPB-ND |  | 5V Buck Controller |  |  | 2.00 | $6.80 | $13.60
296-28778-1-ND |  | 3.3V LDO |  |  | 3.00 | $0.35 | $1.05
P16499CT-ND |  | 180 uF Cap |  |  | 3.00 | $1.39 | $4.17
641-1732-1-ND |  | Buck Con. Diode |  |  | 3.00 | $0.61 | $1.83
SRP1270-100MCT-ND |  | 10uH Inductor |  |  | 2.00 | $1.55 | $3.10
P18927CT-ND |  | 330uF Cap |  |  | 2.00 | $1.86 | $3.72
490-1642-1-ND |  | 0.01uF Cap (0805) |  |  | 3.00 | $0.25 | $0.75
296-9716-5-ND |  | Line Receiver IC |  |  | 1.00 | $6.26 | $6.26
490-1053-1-ND |  | Ferrite Bead |  |  | 10.00 | $0.10 | $0.97
CP-202AH-ND |  | Barrel Jack Connector (24V) |  |  | 1.00 | $0.69 | $0.69
CP-025-ND |  | Barrel Jack Connector (14V) |  |  | 3.00 | $0.74 | $2.22
296-OPA4205APWRCT-ND |  | General Op-Amp (4 channel) |  |  | 2.00 | $6.42 | $12.84
296-40221-1-ND |  | -15V Boost Inverter |  |  | 2.00 | $4.15 | $8.30
445-172950-1-ND |  | 22uH Inductor |  |  | 3.00 | $0.35 | $1.05
493-9695-1-ND |  | 68uF Capacitor |  |  | 3.00 | $0.53 | $1.59
3352T-203LF-ND |  | 20k Potentiometer |  |  | 2.00 | $3.39 | $6.78
296-26653-1-ND |  | NPN Transistor Array |  |  | 4.00 | $0.86 | $3.44
516-1603-5-ND |  | Optocoupler |  |  | 3.00 | $8.67 | $26.01
1N4148WS-13-FDICT-ND |  | 1N4148 Diode |  |  | 12.00 | $0.21 | $2.52
EG5546CT-ND |  | RST Button |  |  | 2.00 | $0.88 | $1.76
350-2046-1-ND |  | Blue LED |  |  | 3.00 | $0.59 | $1.77
160-1738-1-ND |  | White LED |  |  | 3.00 | $0.61 | $1.83
350-2038-1-ND |  | Red LED |  |  | 3.00 | $0.29 | $0.87
350-2044-1-ND |  | Green LED |  |  | 3.00 | $0.29 | $0.87
3565-RS0104YQCT-ND |  | Level Shifter |  |  | 8.00 | $0.67 | $5.36
P680ADCT-ND |  | 680 Ohm 1/2W Resistor |  |  | 3.00 | $0.13 | $0.39
P560ADCT-ND |  | 560 Ohm 1/2W Resistor |  |  | 3.00 | $0.13 | $0.39
DD50P564GTXLF-ND |  | 50 Pin Analog Connector |  |  | 2.00 | $5.82 | $11.64
RMCF0805FT25K5CT-ND |  | 25.5k Resistor |  |  | 24.00 | $0.02 | $0.48
RMCF0805FT75K0CT-ND |  | 75k Resistor |  |  | 27.00 | $0.02 | $0.54
RMCF0805FT105KCT-ND |  | 105k Resistor |  |  | 3.00 | $0.10 | $0.30
541-73.2KCCT-ND |  | 73.2k Resistor |  |  | 15.00 | $0.04 | $0.57
RMCF0805FT1M00CT-ND |  | 1M Resistor |  |  | 3.00 | $0.10 | $0.30
738-RMCF0805FT88K7CT-ND |  | 88.7k Resistor |  |  | 3.00 | $0.10 | $0.30
RMCF0805FT10K0CT-ND |  | 10k Resistor |  |  | 15.00 | $0.02 | $0.30
1712-RA73F2A2K26BTDCT-ND |  | 2.25k Resistor (1W) |  |  | 10.00 | $0.92 | $9.22
RMCF0805FT100RCT-ND |  | 100 Resistor |  |  | 3.00 | $0.10 | $0.30
RMCF0805FT75R0CT-ND |  | 75 Resistor |  |  | 3.00 | $0.10 | $0.30
RMCF0805FT330RCT-ND |  | 330 Resistor |  |  | 24.00 | $0.02 | $0.48
RMCF0805FT499RCT-ND |  | 499 Resistor |  |  | 24.00 | $0.02 | $0.48
RMCF0805FT1K00CT-ND |  | 1k Resistor |  |  | 18.00 | $0.02 | $0.36
1276-6840-1-ND |  | 0.1u Capacitor (X7R) |  |  | 58.00 | $0.03 | $1.59
1276-2561-1-ND |  | 10p Capacitor |  |  | 3.00 | $0.10 | $0.30
1276-1029-1-ND |  | 1u Capacitor |  |  | 50.00 | $0.04 | $2.25
1276-1248-1-ND |  | 4.7u Capacitor (X7R) |  |  | 10.00 | $0.15 | $1.48
1276-2409-1-ND |  | 2.2u Capacitor (X7R) |  |  | 10.00 | $0.18 | $1.78
1276-1039-1-ND |  | 470n Capacitor (X7R) |  |  | 3.00 | $0.10 | $0.30
1276-1201-1-ND |  | 120p Capacitor (X7R) |  |  | 3.00 | $0.10 | $0.30
1276-2891-1-ND |  | 10u Capacitor (X7R) |  |  | 3.00 | $0.18 | $0.54
 |  |  |  |  |  | $0.00 | $0.00
 |  |  |  |  |  | $0.00 | $0.00
 |  |  |  |  |  | $0.00 | $0.00
 |  | TAX |  |  |  | $0.00 | $1.92
Shipping / Handling |  |  |  |  |  | $0.00 | $6.99
Requisition Total |  |  |  |  |  |  | $186.83
*** ALL BLUE CELLS are Mandatory *** Do Not Alter Formulas ***

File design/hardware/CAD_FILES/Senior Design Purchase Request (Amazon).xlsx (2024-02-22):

College of Engineering Senior Design Purchase Request Form |  |  | Department Name: | Today's Date: | 2024-02-21
 |  |  | ECE | Need-By Date: | ASAP
Vendor: | Amazon |  | Team Name / Project: | Your Name: | Ayman Motoda |  |  | <-- Put your name and also your team number in the Your Name: box
Website: | https://www.amazon.com/ |  | ECE 47700 / Team 05 | Building Abbv.: | BHEE
Phone Number: | 1-888-280-4331 |  |  | Room Number: | 007
Vendor Contact: |  |  | Account Number: | Phone Number: | 2405135229 |  |  | <-- Your Phone number
Contact Email: |  |  | 7600000796 | Email Address: | aelnamr@purdue.edu |  |  | <-- Your PURDUE email
ITEM NAME / PART NUMBER |  | DESCRIPTION & LINK |  |  | QUANTITY | UNIT COST | TOTAL COST
DEFY Yellow 10oz Boxing Gloves ‎/ Full Yellow Gloves_1 |  | https://www.amazon.com/DEFY-Training-Punching-Sparring-Kickboxing/dp/B0B7WFHT4B |  |  | 1.00 | $20.99 | $20.99
24V 3A 72W AC to DC Adapter Power Supply / ALT-2403 |  | https://www.amazon.com/ALITOVE-Converter-Transformer-5-5x2-1mm-Computer/dp/B078RY7BPL |  |  | 1.00 | $14.99 | $14.99
 |  |  |  |  |  | $0.00 | $0.00
 |  |  |  |  |  | $0.00 | $0.00
 |  |  |  |  |  | $0.00 | $0.00
 |  |  |  |  |  | $0.00 | $0.00
 |  |  |  |  |  | $0.00 | $0.00
 |  |  |  |  |  | $0.00 | $0.00
 |  |  |  |  |  | $0.00 | $0.00
 |  |  |  |  |  | $0.00 | $0.00
 |  |  |  |  |  | $0.00 | $0.00
 |  |  |  |  |  | $0.00 | $0.00
 |  |  |  |  |  | $0.00 | $0.00
 |  |  |  |  |  | $0.00 | $0.00
 |  |  |  |  |  | $0.00 | $0.00
 |  |  |  |  |  | $0.00 | $0.00
 |  |  |  |  |  | $0.00 | $0.00
 |  |  |  |  |  | $0.00 | $0.00
 |  |  |  |  |  | $0.00 | $0.00
 |  |  |  |  |  | $0.00 | $0.00
 |  | TAX |  |  | 1.00 | $2.52 | $2.52
Shipping / Handling |  |  |  |  |  | $0.00 | $0.00
Requisition Total |  |  |  |  |  |  | $38.50
*** ALL BLUE CELLS are Mandatory *** Do Not Alter Formulas ***

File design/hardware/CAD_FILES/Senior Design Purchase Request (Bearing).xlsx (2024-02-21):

College of Engineering Senior Design Purchase Request Form |  |  | Department Name: | Today's Date: | 2024-02-20
 |  |  | ECE | Need-By Date: | ASAP
Vendor: | Quality Bearings Online |  | Team Name / Project: | Your Name: | Ayman Motoda |  |  | <-- Put your name and also your team number in the Your Name: box
Website: | https://www.qualitybearingsonline.com/ |  | ECE 47700 / Team 05 | Building Abbv.: | BHEE
Phone Number: | 1-646-465-8494 |  |  | Room Number: | 007
Vendor Contact: |  |  | Account Number: | Phone Number: | 2405135229 |  |  | <-- Your Phone number
Contact Email: | sales@qualitybearingsonline.com |  | 7600000796 | Email Address: | aelnamr@purdue.edu |  |  | <-- Your PURDUE email
ITEM NAME / PART NUMBER |  | DESCRIPTION & LINK |  |  | QUANTITY | UNIT COST | TOTAL COST
6209zz-timken |  | 6209 ZZ - Timken Deep Groove Radial Ball Bearing - 45x85x19mm |  |  | 3.00 | $43.01 | $129.03
 |  |  |  |  |  | $0.00 | $0.00
 |  |  |  |  |  | $0.00 | $0.00
 |  |  |  |  |  | $0.00 | $0.00
 |  |  |  |  |  | $0.00 | $0.00
 |  |  |  |  |  | $0.00 | $0.00
 |  |  |  |  |  | $0.00 | $0.00
 |  |  |  |  |  | $0.00 | $0.00
 |  |  |  |  |  | $0.00 | $0.00
 |  |  |  |  |  | $0.00 | $0.00
 |  |  |  |  |  | $0.00 | $0.00
 |  |  |  |  |  | $0.00 | $0.00
 |  |  |  |  |  | $0.00 | $0.00
 |  |  |  |  |  | $0.00 | $0.00
 |  |  |  |  |  | $0.00 | $0.00
 |  |  |  |  |  | $0.00 | $0.00
 |  |  |  |  |  | $0.00 | $0.00
 |  |  |  |  |  | $0.00 | $0.00
 |  |  |  |  |  | $0.00 | $0.00
 |  |  |  |  |  | $0.00 | $0.00
 |  |  |  |  |  | $0.00 | $0.00
Shipping / Handling |  |  |  |  |  | $0.00 | $10.00
Requisition Total |  |  |  |  |  |  | $139.03
*** ALL BLUE CELLS are Mandatory *** Do Not Alter Formulas ***

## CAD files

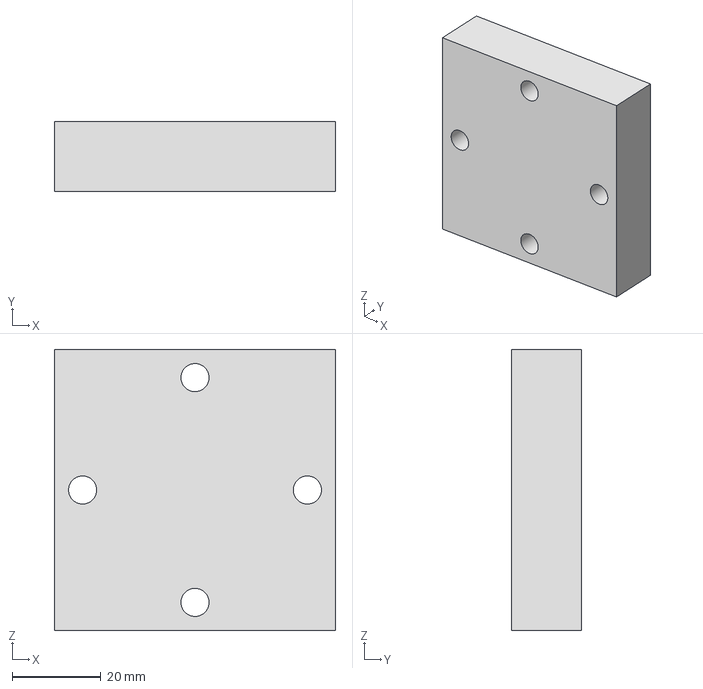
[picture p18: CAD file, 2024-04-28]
design/hardware/CAD_FILES/FrontPlatePostNoKey.stp
63.5 x 15.9 x 63.5 mm

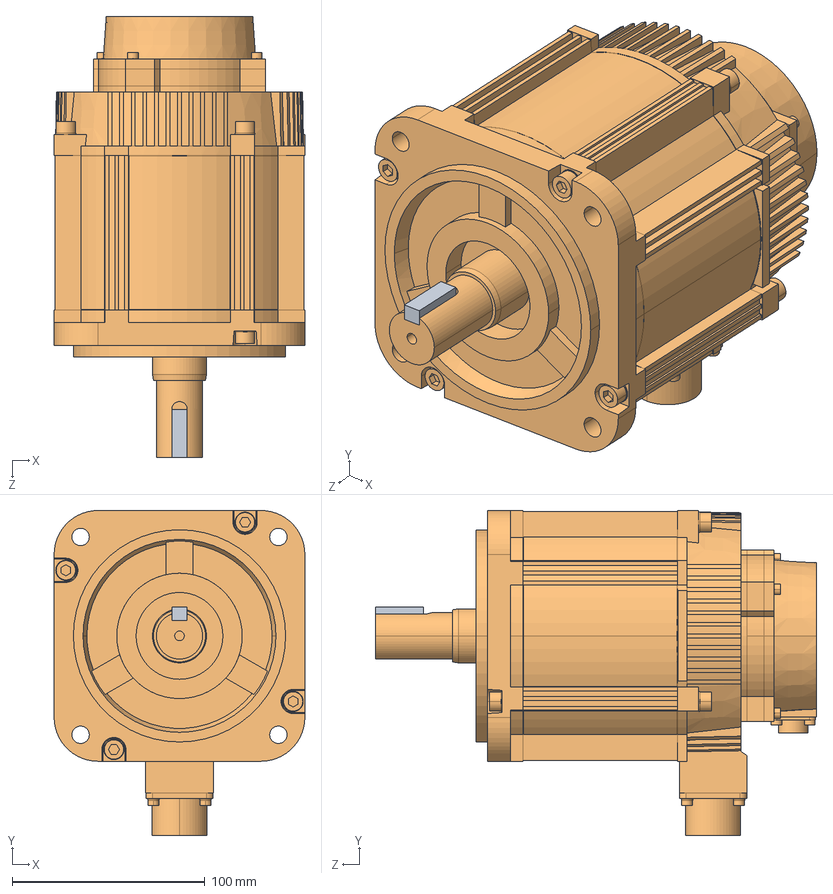
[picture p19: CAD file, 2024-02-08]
design/hardware/CAD_FILES/SGM7G_20AxA61/SGM7G-20xxA61/STEP/SGM7G-20__a61.STEP
130.0 x 168.5 x 228.6 mm
sgm7g_20__a61_key
sgm7g_20__a61_base

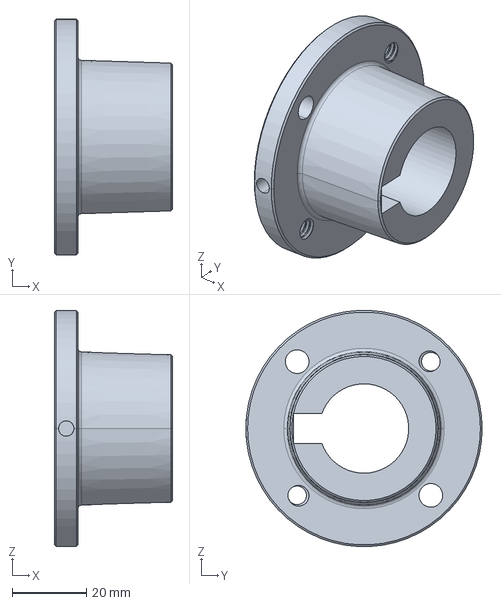
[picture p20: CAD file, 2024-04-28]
design/hardware/CAD_FILES/grainger-small.stp
31.8 x 63.5 x 63.4 mm

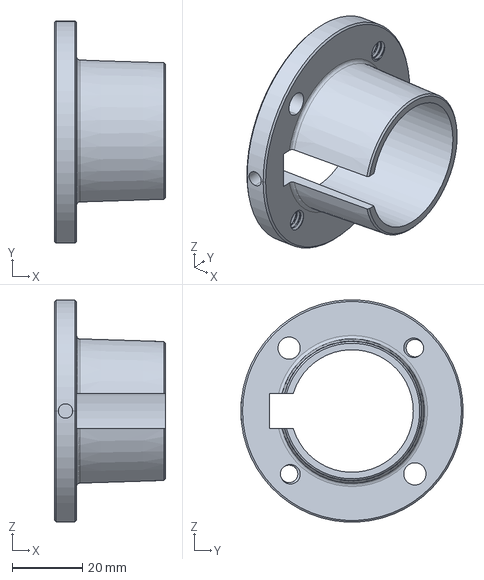
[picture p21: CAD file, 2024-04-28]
design/hardware/CAD_FILES/grainger-big.stp
31.8 x 63.5 x 63.4 mm

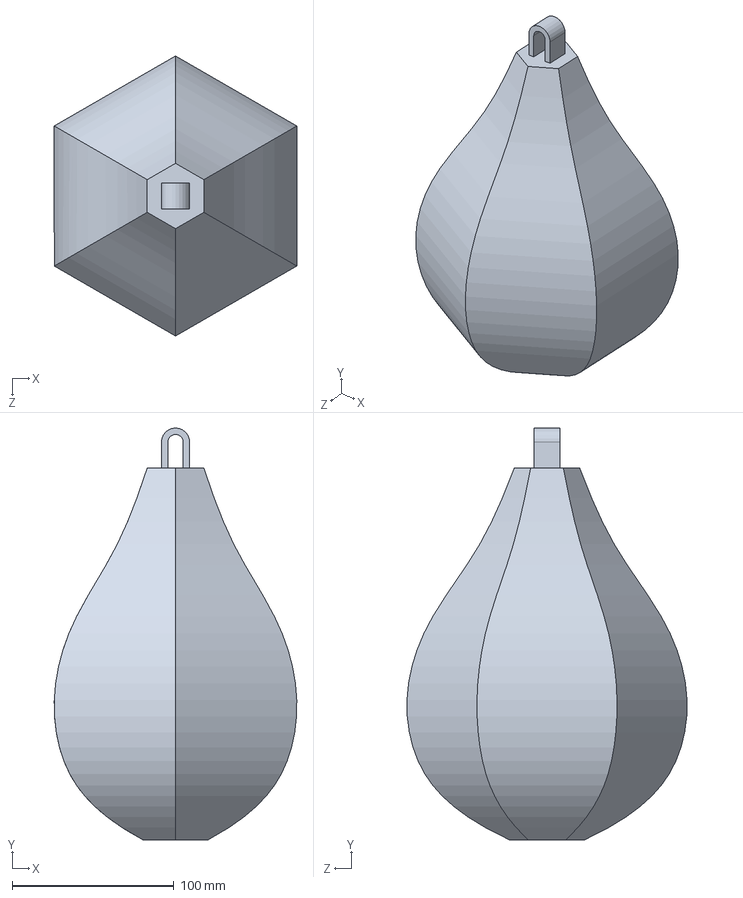
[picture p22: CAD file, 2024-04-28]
design/hardware/CAD_FILES/Speedbag.SLDPRT
150.0 x 254.8 x 173.2 mm

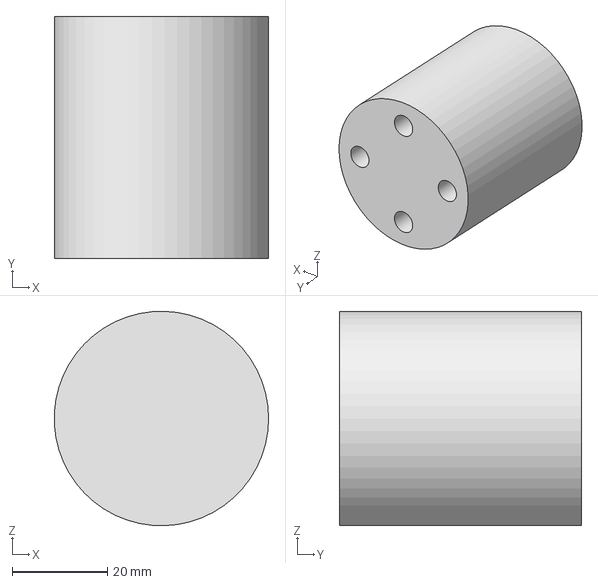
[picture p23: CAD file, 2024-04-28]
design/hardware/CAD_FILES/FrontPlatePostEndSide.stp
45.0 x 50.8 x 45.0 mm

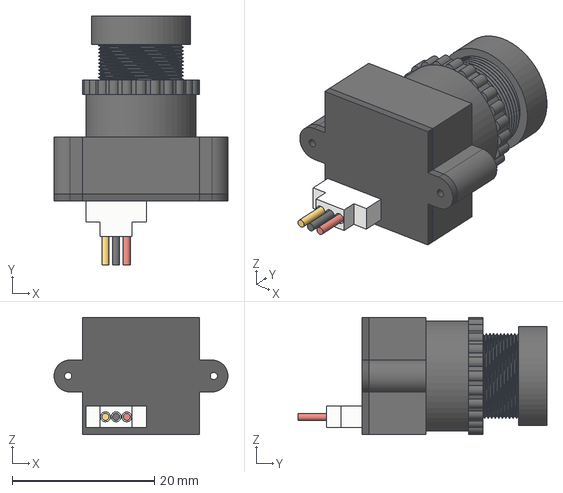
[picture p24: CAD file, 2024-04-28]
design/hardware/CAD_FILES/1000TVL v6.step
24.5 x 35.0 x 16.5 mm

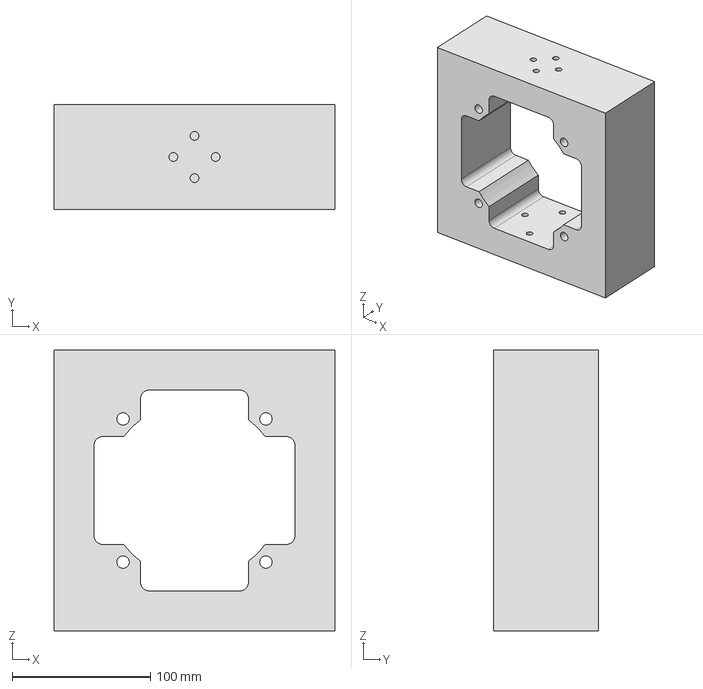
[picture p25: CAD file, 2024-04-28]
design/hardware/CAD_FILES/FrontPlateV3.stp
203.2 x 76.2 x 203.2 mm

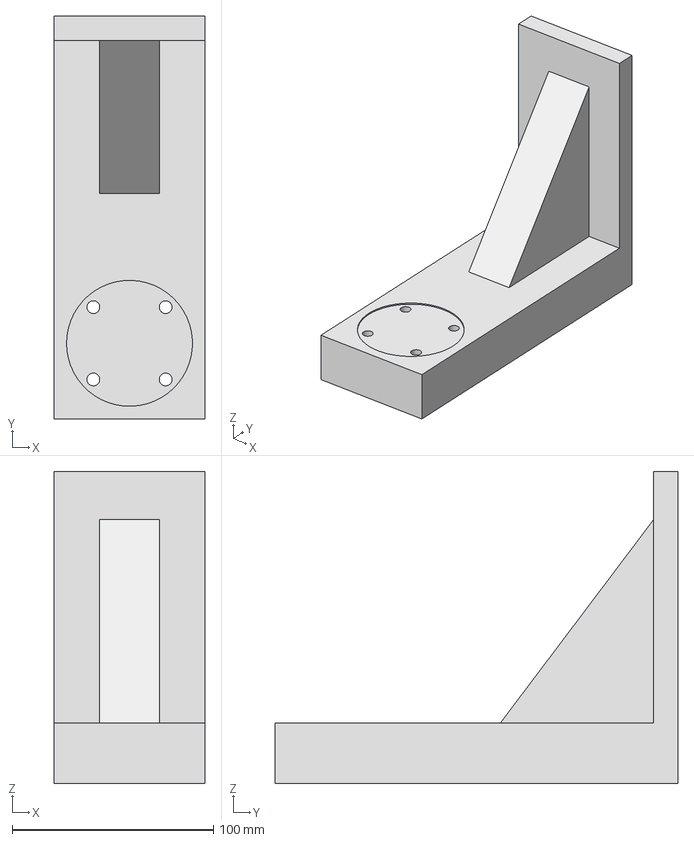
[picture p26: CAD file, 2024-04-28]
design/hardware/CAD_FILES/EndEffector.stp
75.0 x 200.0 x 155.0 mm

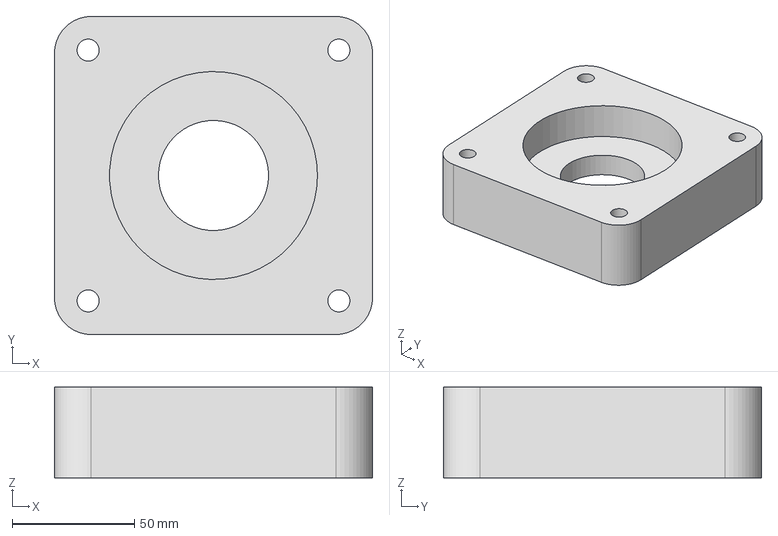
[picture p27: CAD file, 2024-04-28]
design/hardware/CAD_FILES/EndEffectorMotorAdapter.stp
130.0 x 130.0 x 37.0 mm

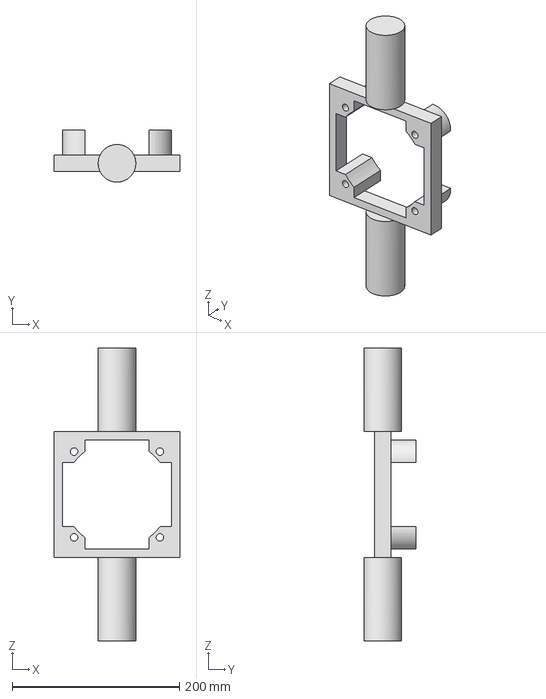
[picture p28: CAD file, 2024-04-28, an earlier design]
design/hardware/CAD_FILES/FrontPlateV2.stp
150.0 x 62.5 x 350.0 mm

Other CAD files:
design/hardware/CAD_FILES/Final AssemblyV5.dwg
design/hardware/CAD_FILES/FloorMount.dwg
design/hardware/CAD_FILES/FloorMountFacePlate.dwg
design/hardware/CAD_FILES/145100992-9-skf_bearing_6209-2z_2/OldVersions/skf_bearing_6209-2z_2.0001.iam
design/hardware/CAD_FILES/145100992-9-skf_bearing_6209-2z_2/OldVersions/skf_bearing_6209-2z_2_01.0001.ipt
design/hardware/CAD_FILES/145100992-9-skf_bearing_6209-2z_2/OldVersions/skf_bearing_6209-2z_2_02.0001.ipt
design/hardware/CAD_FILES/145100992-9-skf_bearing_6209-2z_2/OldVersions/skf_bearing_6209-2z_2_03.0001.ipt
design/hardware/CAD_FILES/145100992-9-skf_bearing_6209-2z_2/OldVersions/skf_bearing_6209-2z_2_04.0001.ipt
design/hardware/CAD_FILES/145100992-9-skf_bearing_6209-2z_2/OldVersions/skf_bearing_6209-2z_2_05.0001.ipt
design/hardware/CAD_FILES/145100992-9-skf_bearing_6209-2z_2/skf_bearing_6209-2z_2.iam
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

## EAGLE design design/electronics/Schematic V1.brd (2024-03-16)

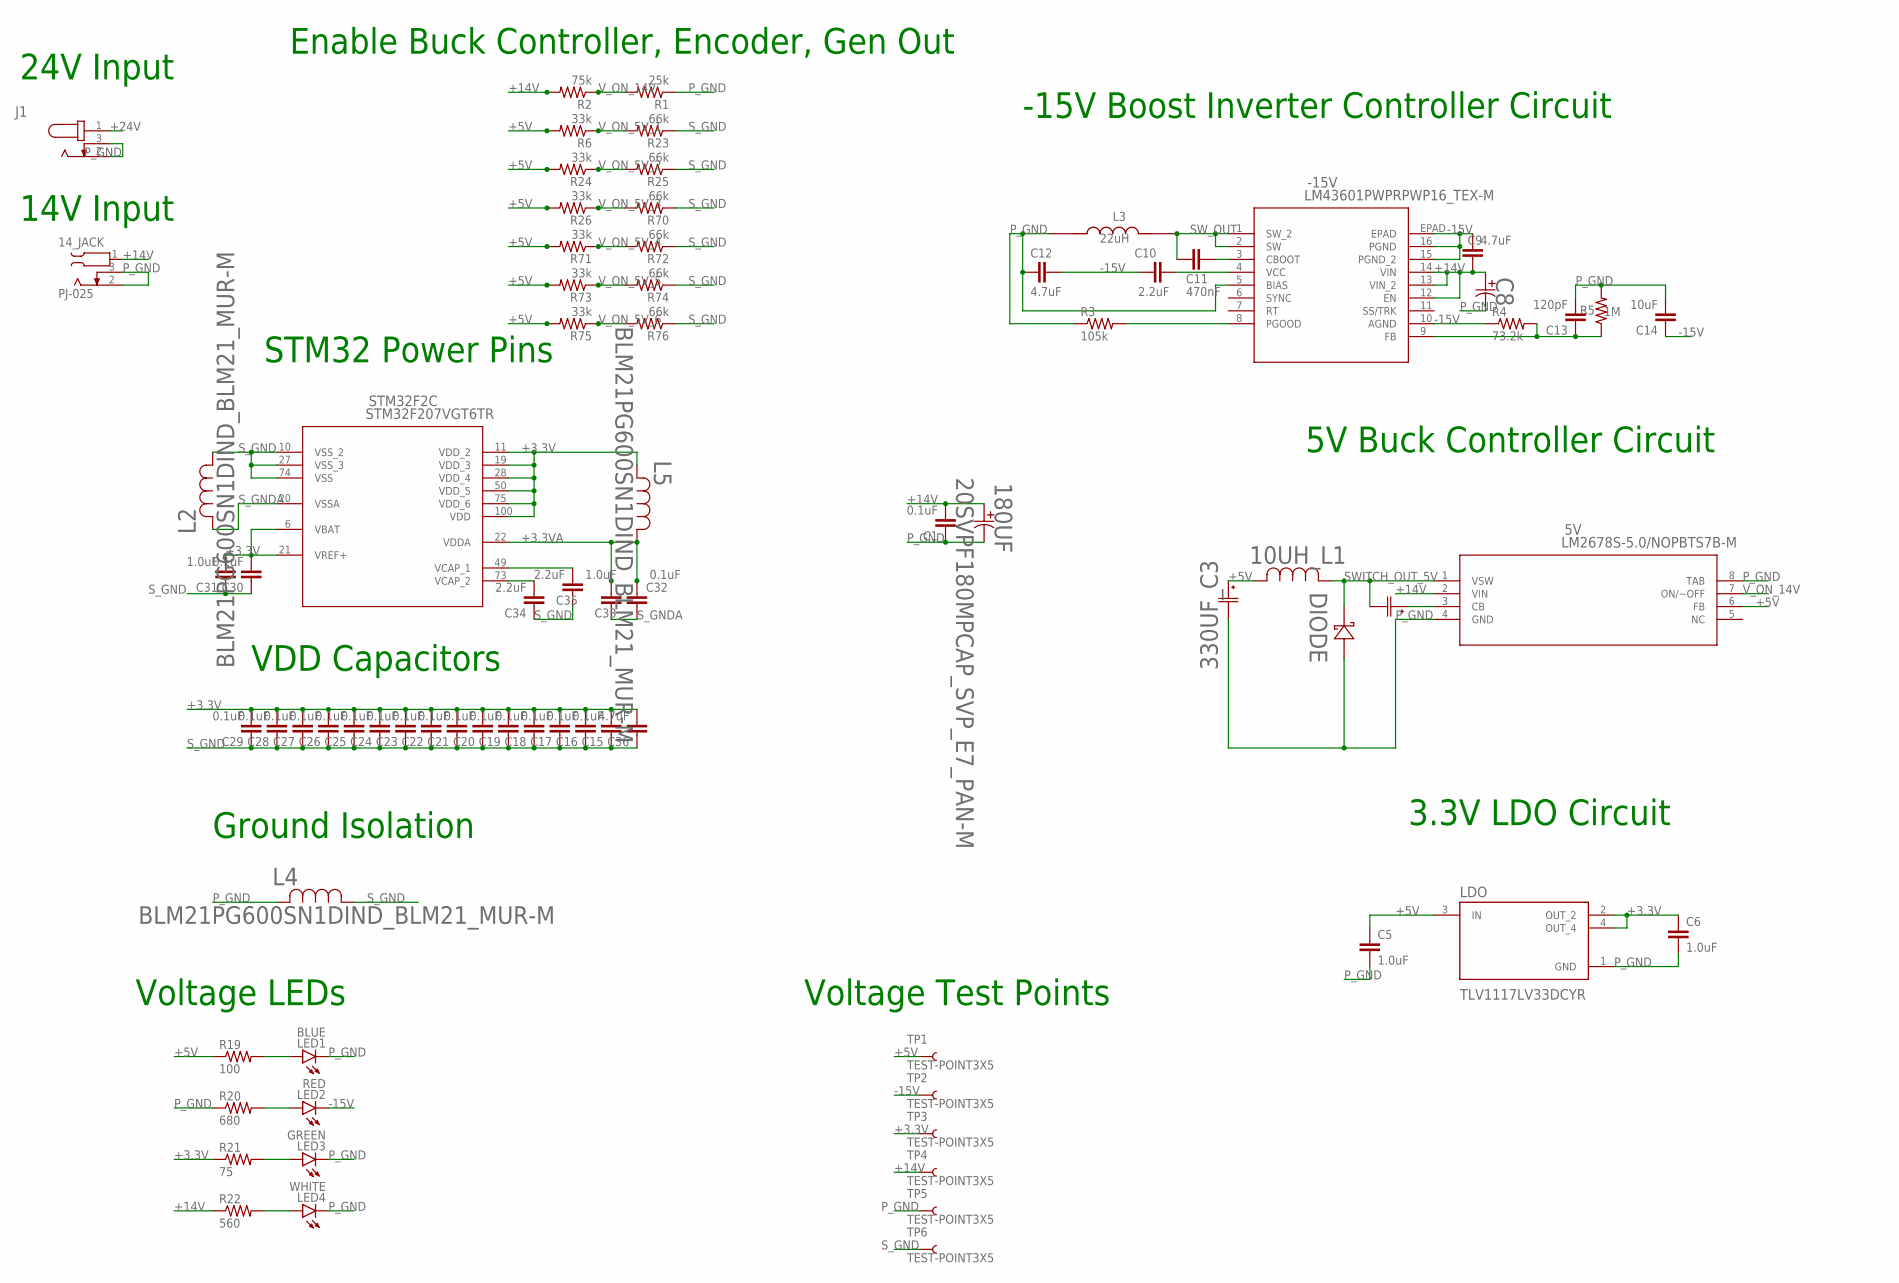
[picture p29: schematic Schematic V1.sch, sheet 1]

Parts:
0.01UF_C7: GRM2195C1H103JA01DG-21_MUR-M; G-21_MUR-M
5V: LM2678S-5.0/NOPBTS7B-M; TS7B-M
10UH_L1: SRP1270-100MIND_BOURNS_SRP1270-M; IND_BOURNS_SRP1270-M
14_JACK: PJ-025; CUI_PJ-025
180UF: 20SVPF180MPCAP_SVP_E7_PAN-M; PCAP_SVP_E7_PAN-M
330UF_C3: 10SVPC330MCAP_SVPC_E7_PAN-M; CAP_SVPC_E7_PAN-M
-15V: LM43601PWPRPWP16_TEX-M; PWP16_TEX-M
C1, C15, C16, C17, C18, C19, C20, C21, C22, C23, C24, C25, C26, C27, C28, C29, C30, C32: 0.1uF; 0805
C5, C6, C31, C33: 1.0uF; 0805
C8: 68uF; PCAP_6.3X7.7-ELECT_NCA-M
C9, C12, C36: 4.7uF; 0805
C10, C34, C35: 2.2uF; 0805
C11: 470nF; 0805
C13: 120pF; 0805
C14: 10uF; 0805
DIODE: CDBC520-GCDBC-G-M; CDBC-G-M
J1: PJ-202AH; CUI_PJ-202AH
L2, L4, L5: BLM21PG600SN1DIND_BLM21_MUR-M; IND_BLM21_MUR-M
L3: 22uH; IND_VLS201610CX-220M-1
LDO: TLV1117LV33DCYR; VREG_TLV1117LV33DCYR
LED1: BLUE; CHIPLED_0805
LED2: RED; CHIPLED_0805
LED3: GREEN; CHIPLED_0805
LED4: WHITE; CHIPLED_0805
R1: 25k; R0805
R2: 75k; R0805
R3: 105k; R0805
R4: 73.2k; R0805
R5: 1M; R0805
R6, R24, R26, R71, R73, R75: 33k; R0805
R19: 100; R0805
R20: 680; R0805
R21: 75; R0805
R22: 560; R0805
R23, R25, R70, R72, R74, R76: 66k; R0805
STM32F2: STM32F207VGT6TR; LQFP100-14X14MM
TP1, TP2, TP3, TP4, TP5, TP6: TEST-POINT3X5; PAD.03X.05

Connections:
+3.3V: C6.1, C15.2, C16.2, C17.2, C18.2, C19.2, C20.2, C21.2, C22.2, C23.2, C24.2, C25.2, C26.2, C27.2, C28.2, C29.2, C30.2, C31.2, C36.2, L5.2, LDO.2 (OUT_2), LDO.4 (OUT_4), R21.1, STM32F2.6 (VBAT), STM32F2.11 (VDD_2), STM32F2.19 (VDD_3), STM32F2.21 (VREF+), STM32F2.28 (VDD_4), STM32F2.50 (VDD_5), STM32F2.75 (VDD_6), STM32F2.100 (VDD), TP3.1; also elsewhere on the board
+3.3VA: C32.2, C33.2, L5.1, STM32F2.22 (VDDA)
+5V: 5V.6 (FB), 10UH_L1.2, 330UF_C3.1, C5.1, LDO.3 (IN), R6.2, R19.1, R24.2, R26.2, R71.2, R73.2, R75.2, TP1.1; also elsewhere on the board
+14V: 5V.2 (VIN), 14_JACK.1, 180UF.1, -15V.12 (EN), -15V.13 (VIN_2), -15V.14 (VIN), C1.2, C8.1, C9.2, R2.2, R22.1, TP4.1; also elsewhere on the board
+24V: J1.1; also elsewhere on the board
-15V: -15V.10 (AGND), -15V.15 (PGND_2), -15V.16 (PGND), -15V.EPAD, C9.1, C10.1, C12.1, C14.1, LED2.C, R4.1, TP2.1; also elsewhere on the board
unnamed: -15V.4 (VCC), C10.2
unnamed: 0.01UF_C7.1, 5V.3 (CB)
unnamed: -15V.3 (CBOOT), C11.2
unnamed: C35.2, STM32F2.49 (VCAP_1)
unnamed: C34.2, STM32F2.73 (VCAP_2)
unnamed: -15V.8 (PGOOD), R3.2
unnamed: -15V.9 (FB), C13.1, R4.2, R5.1
unnamed: LED1.A, R19.2
unnamed: LED2.A, R20.2
unnamed: LED3.A, R21.2
unnamed: LED4.A, R22.2
P_GND: 5V.4 (GND), 5V.8 (TAB), 14_JACK.2, 14_JACK.3, 180UF.2, 330UF_C3.2, -15V.5 (BIAS), C1.1, C5.2, C6.2, C8.2, C12.2, C13.2, C14.2, DIODE.2, J1.2, J1.3, L3.1, L4.2, LDO.1 (GND), LED1.C, LED3.C, LED4.C, R1.1, R3.1, R5.2, R20.1, TP5.1; also elsewhere on the board
SWITCH_OUT_5V: 0.01UF_C7.2, 5V.1 (VSW), 10UH_L1.1, DIODE.1
SW_OUT: -15V.1 (SW_2), -15V.2 (SW), C11.1, L3.2
S_GND: C15.1, C16.1, C17.1, C18.1, C19.1, C20.1, C21.1, C22.1, C23.1, C24.1, C25.1, C26.1, C27.1, C28.1, C29.1, C30.1, C31.1, C34.1, C35.1, C36.1, L2.1, L4.1, R23.1, R25.1, R70.1, R72.1, R74.1, R76.1, STM32F2.10 (VSS_2), STM32F2.27 (VSS_3), STM32F2.74 (VSS), TP6.1; also elsewhere on the board
S_GNDA: C32.1, C33.1, L2.2, STM32F2.20 (VSSA)
V_ON_5V_1: R6.1, R23.2; also elsewhere on the board
V_ON_5V_2: R24.1, R25.2; also elsewhere on the board
V_ON_5V_3: R26.1, R70.2; also elsewhere on the board
V_ON_5V_4: R71.1, R72.2; also elsewhere on the board
V_ON_5V_5: R73.1, R74.2; also elsewhere on the board
V_ON_5V_6: R75.1, R76.2; also elsewhere on the board
V_ON_14V: 5V.7 (ON/~OFF), R1.2, R2.1

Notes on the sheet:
VDD Capacitors
STM32 Power Pins
5V Buck Controller Circuit
3.3V LDO Circuit
-15V Boost Inverter Controller Circuit
Enable Buck Controller, Encoder, Gen Out
Ground Isolation
Voltage LEDs
Voltage Test Points
14V Input
24V Input

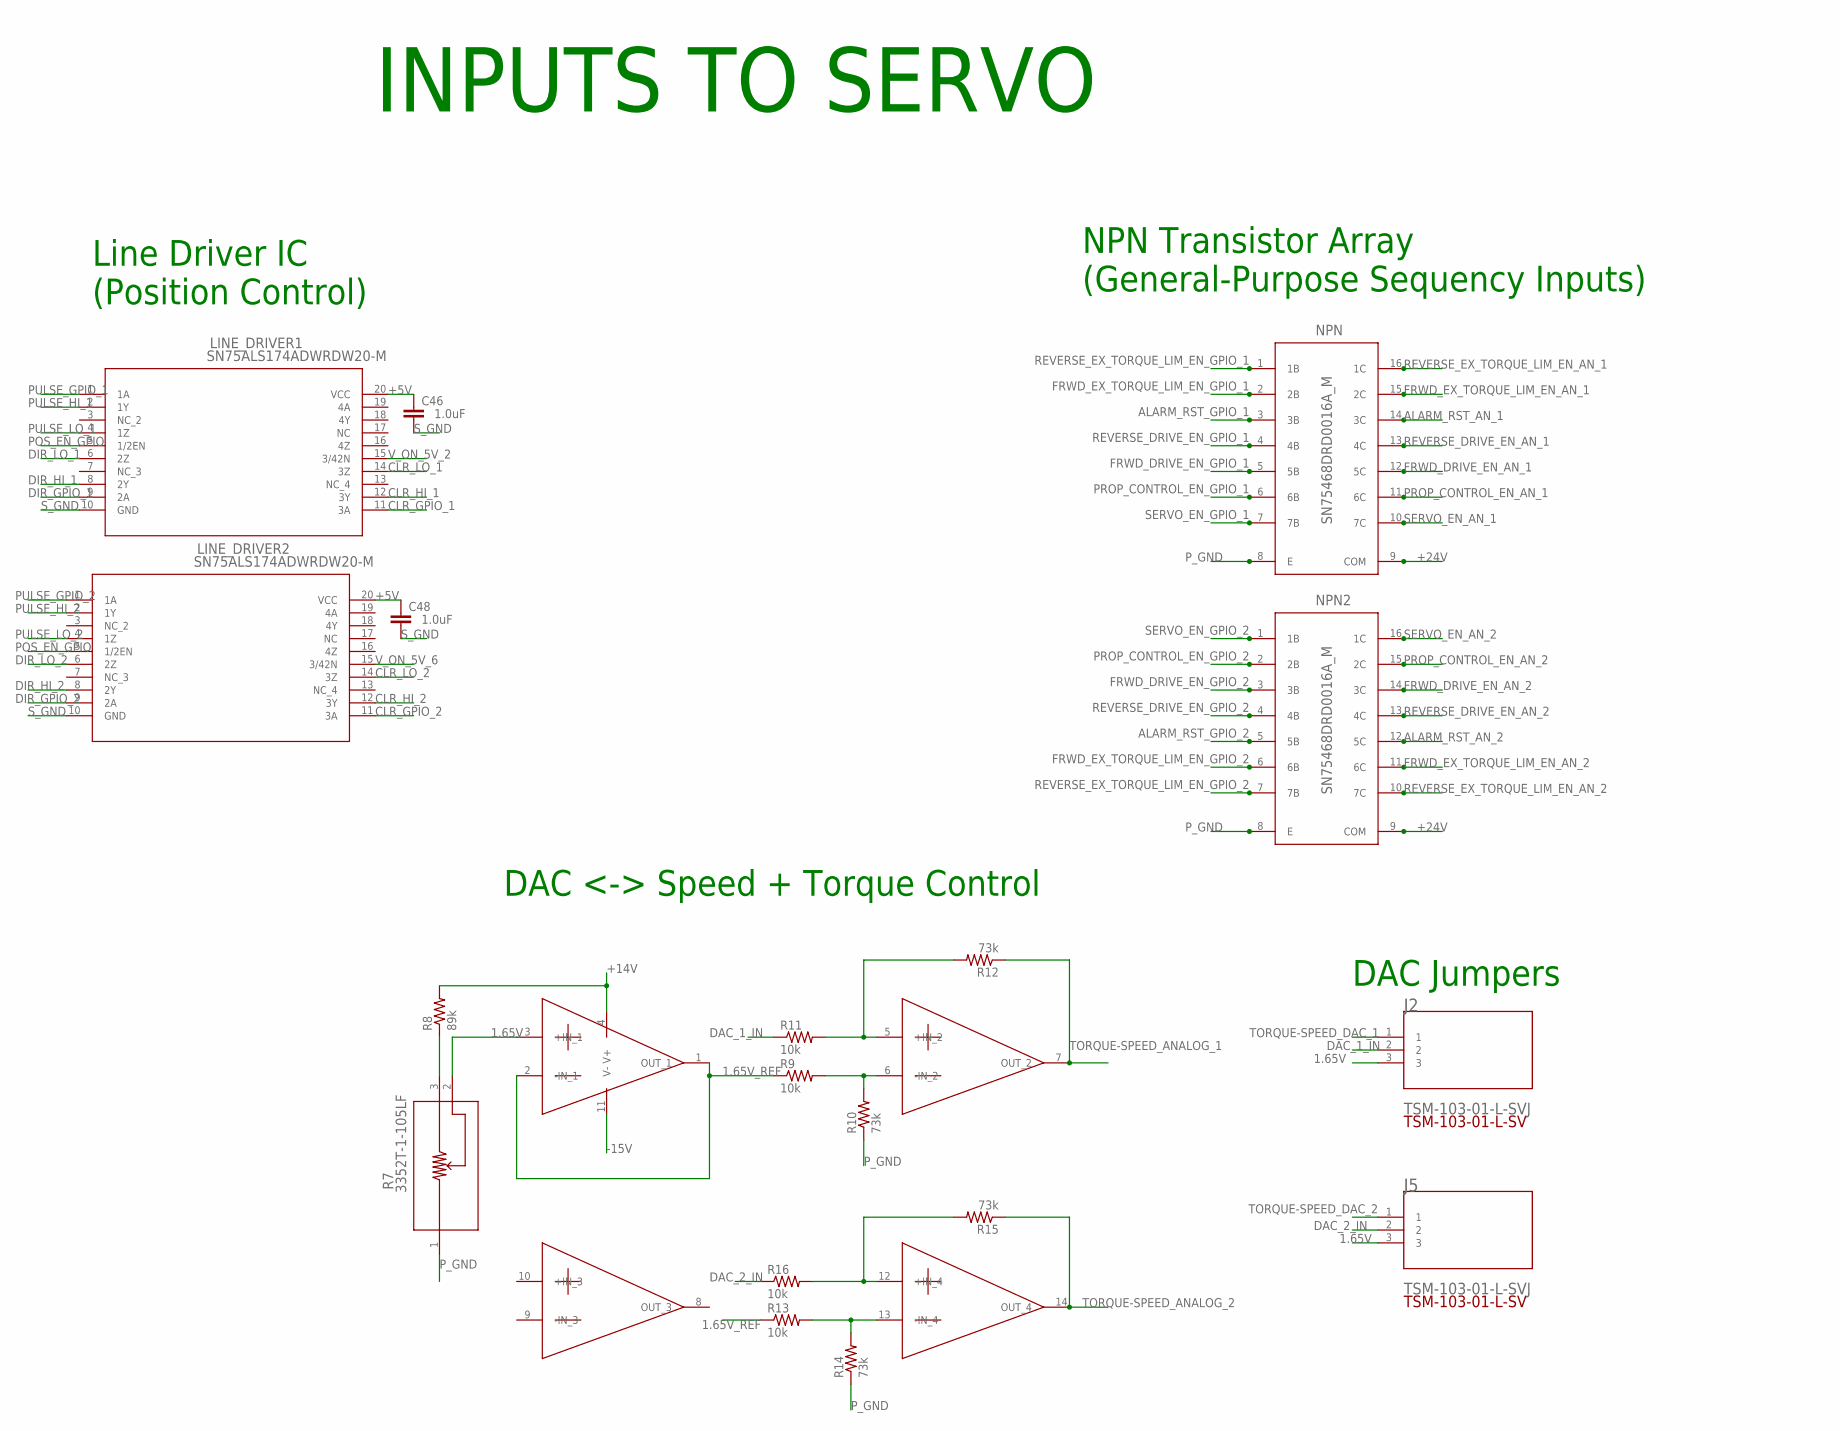
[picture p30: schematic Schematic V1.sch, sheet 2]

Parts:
C46, C48: 1.0uF; 0805
J2, J5: TSM-103-01-L-SVJ; TSM-103-01-L-SV
LINE_DRIVER1, LINE_DRIVER2: SN75ALS174ADWRDW20-M; DW20-M
NPN, NPN2: SN75468DRD0016A_M; D0016A_M
OP_AMP: OPA4205APWRTSSOP14_PW_R-PDSO-G14_TEX-M; TSSOP14_PW_R-PDSO-G14_TEX-M
R7: 3352T-1-105LF; 3352T_BRN
R8: 89k; R0805
R9, R11, R13, R16: 10k; R0805
R10, R12, R14, R15: 73k; R0805

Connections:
1.65V: J2.3, J5.3, OP_AMP.3 (+IN_1), R7.2
1.65V_REF: OP_AMP.1 (OUT_1), OP_AMP.2 (-IN_1), R9.1, R13.1
+5V: C46.2, C48.2, LINE_DRIVER1.20 (VCC), LINE_DRIVER2.20 (VCC); also elsewhere on the board
+14V: OP_AMP.4 (V+), R8.2; also elsewhere on the board
+24V: NPN.9 (COM), NPN2.9 (COM); also elsewhere on the board
-15V: OP_AMP.11 (V-); also elsewhere on the board
ALARM_RST_AN_1: NPN.14 (3C); also elsewhere on the board
ALARM_RST_AN_2: NPN2.12 (5C); also elsewhere on the board
ALARM_RST_GPIO_1: NPN.3 (3B); also elsewhere on the board
ALARM_RST_GPIO_2: NPN2.5 (5B); also elsewhere on the board
CLR_GPIO_1: LINE_DRIVER1.11 (3A); also elsewhere on the board
CLR_GPIO_2: LINE_DRIVER2.11 (3A); also elsewhere on the board
CLR_HI_1: LINE_DRIVER1.12 (3Y); also elsewhere on the board
CLR_HI_2: LINE_DRIVER2.12 (3Y); also elsewhere on the board
CLR_LO_1: LINE_DRIVER1.14 (3Z); also elsewhere on the board
CLR_LO_2: LINE_DRIVER2.14 (3Z); also elsewhere on the board
DAC_1_IN: J2.2, R11.1
DAC_2_IN: J5.2, R16.1
DIR_GPIO_1: LINE_DRIVER1.9 (2A); also elsewhere on the board
DIR_GPIO_2: LINE_DRIVER2.9 (2A); also elsewhere on the board
DIR_HI_1: LINE_DRIVER1.8 (2Y); also elsewhere on the board
DIR_HI_2: LINE_DRIVER2.8 (2Y); also elsewhere on the board
DIR_LO_1: LINE_DRIVER1.6 (2Z); also elsewhere on the board
DIR_LO_2: LINE_DRIVER2.6 (2Z); also elsewhere on the board
FRWD_DRIVE_EN_AN_1: NPN.12 (5C); also elsewhere on the board
FRWD_DRIVE_EN_AN_2: NPN2.14 (3C); also elsewhere on the board
FRWD_DRIVE_EN_GPIO_1: NPN.5 (5B); also elsewhere on the board
FRWD_DRIVE_EN_GPIO_2: NPN2.3 (3B); also elsewhere on the board
FRWD_EX_TORQUE_LIM_EN_AN_1: NPN.15 (2C); also elsewhere on the board
FRWD_EX_TORQUE_LIM_EN_AN_2: NPN2.11 (6C); also elsewhere on the board
FRWD_EX_TORQUE_LIM_EN_GPIO_1: NPN.2 (2B); also elsewhere on the board
FRWD_EX_TORQUE_LIM_EN_GPIO_2: NPN2.6 (6B); also elsewhere on the board
unnamed: OP_AMP.6 (-IN_2), R9.2, R10.2
unnamed: R7.3, R8.1
unnamed: OP_AMP.5 (+IN_2), R11.2, R12.2
unnamed: OP_AMP.13 (-IN_4), R13.2, R14.2
unnamed: OP_AMP.12 (+IN_4), R15.2, R16.2
POS_EN_GPIO: LINE_DRIVER1.5 (1/2EN), LINE_DRIVER2.5 (1/2EN); also elsewhere on the board
PROP_CONTROL_EN_AN_1: NPN.11 (6C); also elsewhere on the board
PROP_CONTROL_EN_AN_2: NPN2.15 (2C); also elsewhere on the board
PROP_CONTROL_EN_GPIO_1: NPN.6 (6B); also elsewhere on the board
PROP_CONTROL_EN_GPIO_2: NPN2.2 (2B); also elsewhere on the board
PULSE_GPIO_1: LINE_DRIVER1.1 (1A); also elsewhere on the board
PULSE_GPIO_2: LINE_DRIVER2.1 (1A); also elsewhere on the board
PULSE_HI_1: LINE_DRIVER1.2 (1Y); also elsewhere on the board
PULSE_HI_2: LINE_DRIVER2.2 (1Y); also elsewhere on the board
PULSE_LO_1: LINE_DRIVER1.4 (1Z); also elsewhere on the board
PULSE_LO_2: LINE_DRIVER2.4 (1Z); also elsewhere on the board
P_GND: NPN.8 (E), NPN2.8 (E), R7.1, R10.1, R14.1; also elsewhere on the board
REVERSE_DRIVE_EN_AN_1: NPN.13 (4C); also elsewhere on the board
REVERSE_DRIVE_EN_AN_2: NPN2.13 (4C); also elsewhere on the board
REVERSE_DRIVE_EN_GPIO_1: NPN.4 (4B); also elsewhere on the board
REVERSE_DRIVE_EN_GPIO_2: NPN2.4 (4B); also elsewhere on the board
REVERSE_EX_TORQUE_LIM_EN_AN_1: NPN.16 (1C); also elsewhere on the board
REVERSE_EX_TORQUE_LIM_EN_AN_2: NPN2.10 (7C); also elsewhere on the board
REVERSE_EX_TORQUE_LIM_EN_GPIO_1: NPN.1 (1B); also elsewhere on the board
REVERSE_EX_TORQUE_LIM_EN_GPIO_2: NPN2.7 (7B); also elsewhere on the board
SERVO_EN_AN_1: NPN.10 (7C); also elsewhere on the board
SERVO_EN_AN_2: NPN2.16 (1C); also elsewhere on the board
SERVO_EN_GPIO_1: NPN.7 (7B); also elsewhere on the board
SERVO_EN_GPIO_2: NPN2.1 (1B); also elsewhere on the board
S_GND: C46.1, C48.1, LINE_DRIVER1.10 (GND), LINE_DRIVER2.10 (GND); also elsewhere on the board
TORQUE-SPEED_ANALOG_1: OP_AMP.7 (OUT_2), R12.1; also elsewhere on the board
TORQUE-SPEED_ANALOG_2: OP_AMP.14 (OUT_4), R15.1; also elsewhere on the board
TORQUE-SPEED_DAC_1: J2.1; also elsewhere on the board
TORQUE-SPEED_DAC_2: J5.1; also elsewhere on the board
V_ON_5V_2: LINE_DRIVER1.15 (3/42N); also elsewhere on the board
V_ON_5V_6: LINE_DRIVER2.15 (3/42N); also elsewhere on the board

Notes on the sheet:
Line Driver IC (Position Control)
DAC <-> Speed + Torque Control
INPUTS TO SERVO
NPN Transistor Array (General-Purpose Sequency Inputs)
DAC Jumpers

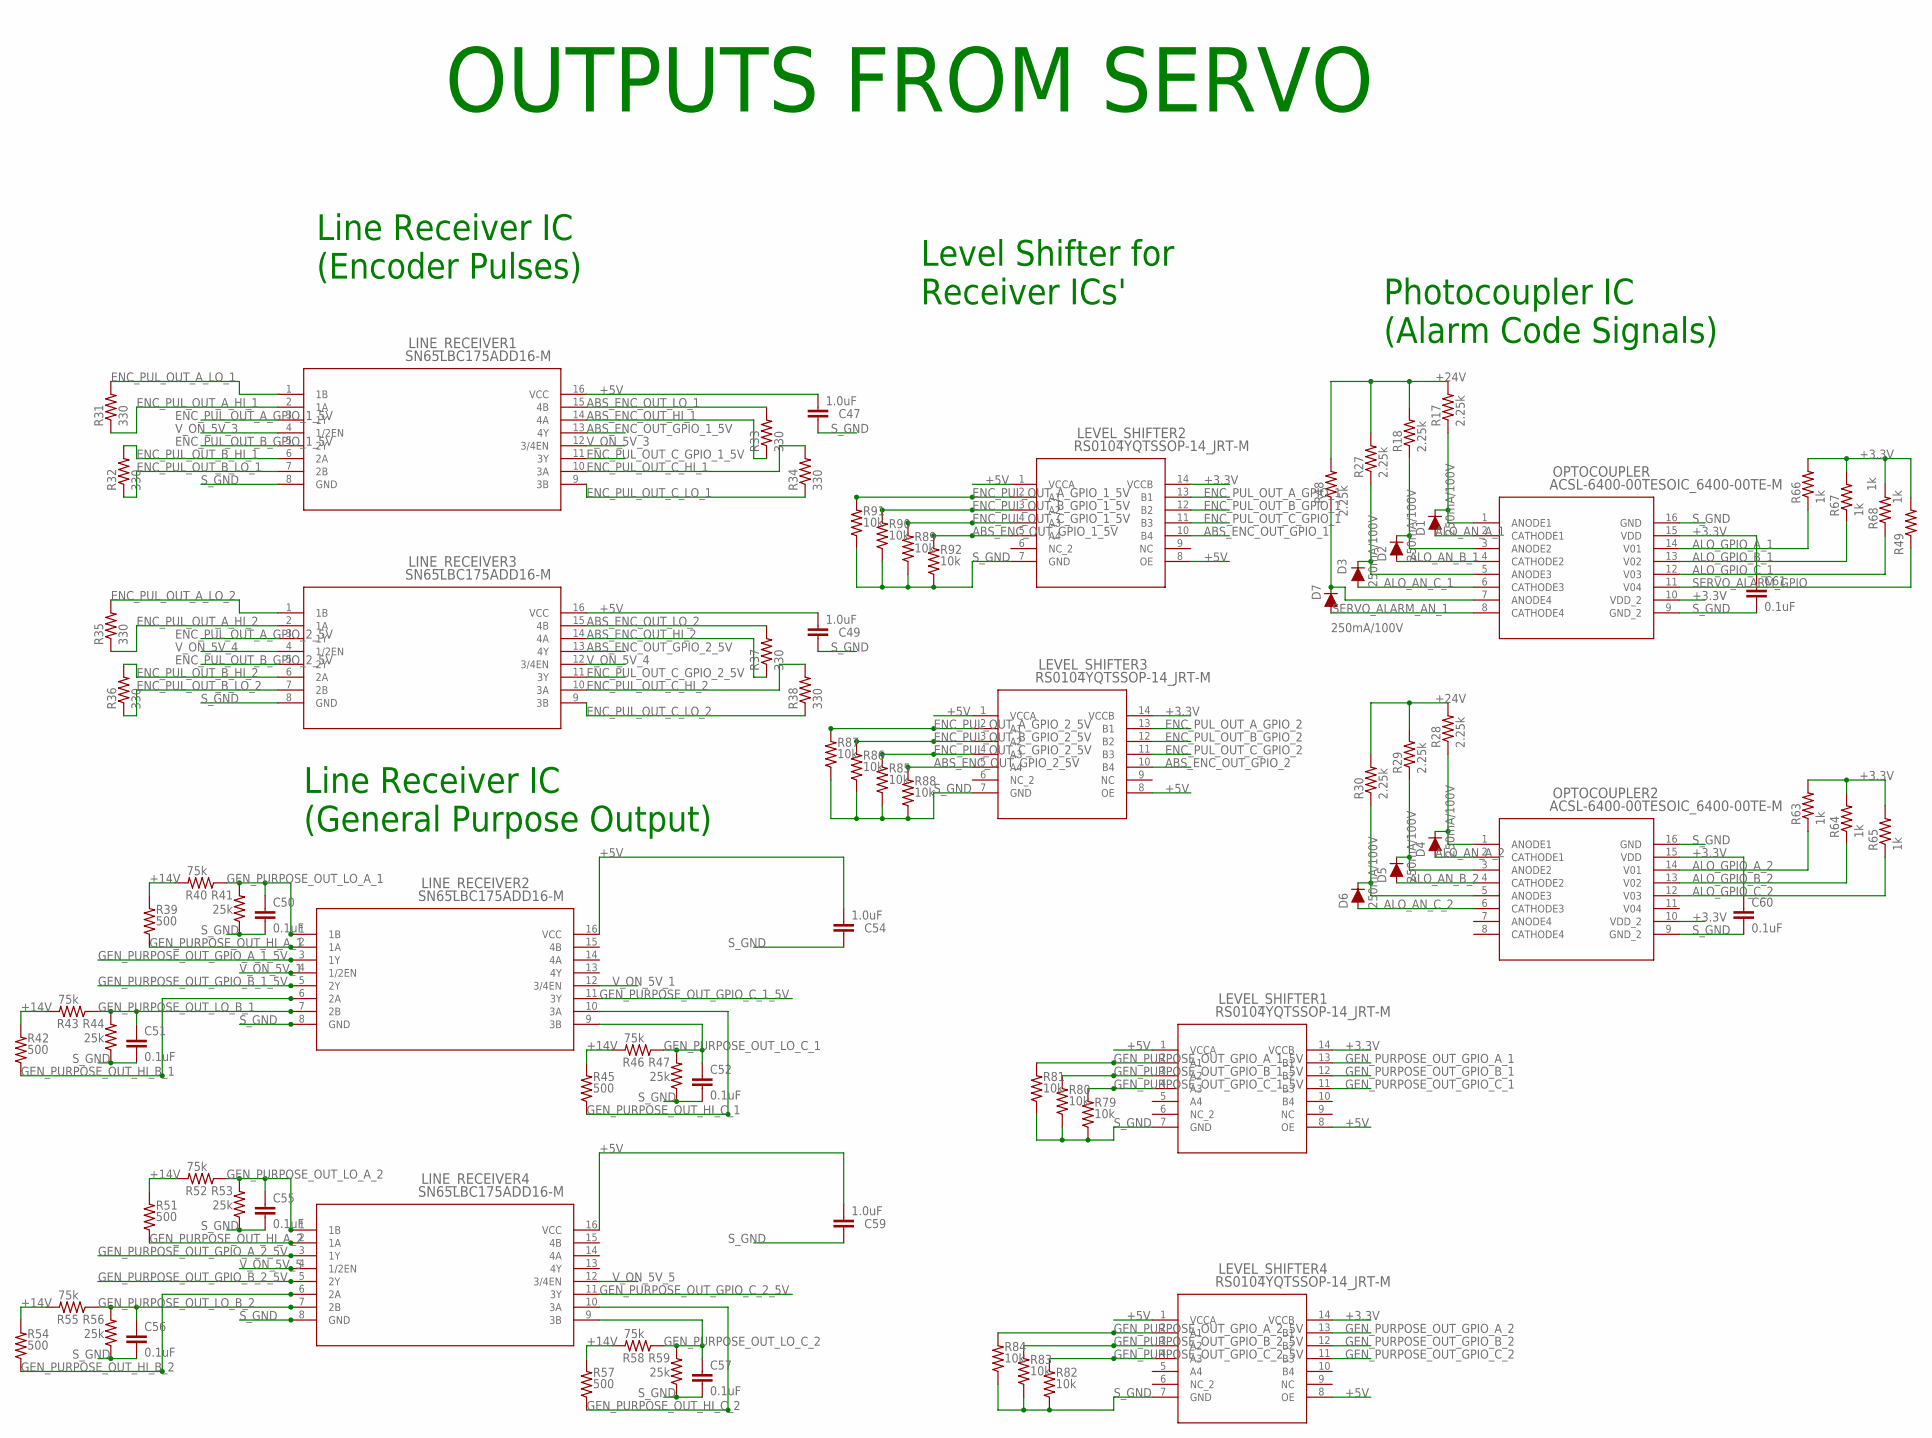
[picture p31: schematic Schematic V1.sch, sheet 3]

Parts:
C47, C49, C54, C59: 1.0uF; 0805
C50, C51, C52, C55, C56, C57, C60, C61: 0.1uF; 0805
D1, D2, D3, D4, D5, D6, D7: 250mA/100V; SOD-323
LEVEL_SHIFTER1, LEVEL_SHIFTER2, LEVEL_SHIFTER3, LEVEL_SHIFTER4: RS0104YQTSSOP-14_JRT-M; TSSOP-14_JRT-M
LINE_RECEIVER1, LINE_RECEIVER2, LINE_RECEIVER3, LINE_RECEIVER4: SN65LBC175ADD16-M; D16-M
OPTOCOUPLER, OPTOCOUPLER2: ACSL-6400-00TESOIC_6400-00TE-M; SOIC_6400-00TE-M
R17, R18, R27, R28, R29, R30, R48: 2.25k; R0805
R31, R32, R33, R34, R35, R36, R37, R38: 330; R0805
R39, R42, R45, R51, R54, R57: 500; R0805
R40, R43, R46, R52, R55, R58: 75k; R0805
R41, R44, R47, R53, R56, R59: 25k; R0805
R49, R63, R64, R65, R66, R67, R68: 1k; R0805
R79, R80, R81, R82, R83, R84, R85, R86, R87, R88, R89, R90, R91, R92: 10k; R0805

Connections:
+3.3V: C60.2, C61.2, LEVEL_SHIFTER1.14 (VCCB), LEVEL_SHIFTER2.14 (VCCB), LEVEL_SHIFTER3.14 (VCCB), LEVEL_SHIFTER4.14 (VCCB), OPTOCOUPLER.10 (VDD_2), OPTOCOUPLER.15 (VDD), OPTOCOUPLER2.10 (VDD_2), OPTOCOUPLER2.15 (VDD), R49.2, R63.2, R64.2, R65.2, R66.2, R67.2, R68.2; also elsewhere on the board
+5V: C47.2, C49.2, C54.2, C59.2, LEVEL_SHIFTER1.1 (VCCA), LEVEL_SHIFTER1.8 (OE), LEVEL_SHIFTER2.1 (VCCA), LEVEL_SHIFTER2.8 (OE), LEVEL_SHIFTER3.1 (VCCA), LEVEL_SHIFTER3.8 (OE), LEVEL_SHIFTER4.1 (VCCA), LEVEL_SHIFTER4.8 (OE), LINE_RECEIVER1.16 (VCC), LINE_RECEIVER2.16 (VCC), LINE_RECEIVER3.16 (VCC), LINE_RECEIVER4.16 (VCC); also elsewhere on the board
+14V: R39.2, R40.2, R42.2, R43.2, R45.2, R46.2, R51.2, R52.2, R54.2, R55.2, R57.2, R58.2; also elsewhere on the board
+24V: R17.2, R18.2, R27.2, R28.2, R29.2, R30.2, R48.2; also elsewhere on the board
ABS_ENC_OUT_GPIO_1: LEVEL_SHIFTER2.10 (B4); also elsewhere on the board
ABS_ENC_OUT_GPIO_1_5V: LEVEL_SHIFTER2.5 (A4), LINE_RECEIVER1.13 (4Y), R92.2
ABS_ENC_OUT_GPIO_2: LEVEL_SHIFTER3.10 (B4); also elsewhere on the board
ABS_ENC_OUT_GPIO_2_5V: LEVEL_SHIFTER3.5 (A4), LINE_RECEIVER3.13 (4Y), R88.2
ABS_ENC_OUT_HI_1: LINE_RECEIVER1.14 (4A), R33.1; also elsewhere on the board
ABS_ENC_OUT_HI_2: LINE_RECEIVER3.14 (4A), R37.1; also elsewhere on the board
ABS_ENC_OUT_LO_1: LINE_RECEIVER1.15 (4B), R33.2; also elsewhere on the board
ABS_ENC_OUT_LO_2: LINE_RECEIVER3.15 (4B), R37.2; also elsewhere on the board
ALO_AN_A_1: D1.A, OPTOCOUPLER.2 (CATHODE1); also elsewhere on the board
ALO_AN_A_2: D4.A, OPTOCOUPLER2.2 (CATHODE1); also elsewhere on the board
ALO_AN_B_1: D2.A, OPTOCOUPLER.4 (CATHODE2); also elsewhere on the board
ALO_AN_B_2: D5.A, OPTOCOUPLER2.4 (CATHODE2); also elsewhere on the board
ALO_AN_C_1: D3.A, OPTOCOUPLER.6 (CATHODE3); also elsewhere on the board
ALO_AN_C_2: D6.A, OPTOCOUPLER2.6 (CATHODE3); also elsewhere on the board
ALO_GPIO_A_1: OPTOCOUPLER.14 (V01), R66.1; also elsewhere on the board
ALO_GPIO_A_2: OPTOCOUPLER2.14 (V01), R63.1; also elsewhere on the board
ALO_GPIO_B_1: OPTOCOUPLER.13 (V02), R67.1; also elsewhere on the board
ALO_GPIO_B_2: OPTOCOUPLER2.13 (V02), R64.1; also elsewhere on the board
ALO_GPIO_C_1: OPTOCOUPLER.12 (V03), R68.1; also elsewhere on the board
ALO_GPIO_C_2: OPTOCOUPLER2.12 (V03), R65.1; also elsewhere on the board
ENC_PUL_OUT_A_GPIO_1: LEVEL_SHIFTER2.13 (B1); also elsewhere on the board
ENC_PUL_OUT_A_GPIO_1_5V: LEVEL_SHIFTER2.2 (A1), LINE_RECEIVER1.3 (1Y), R91.2
ENC_PUL_OUT_A_GPIO_2: LEVEL_SHIFTER3.13 (B1); also elsewhere on the board
ENC_PUL_OUT_A_GPIO_2_5V: LEVEL_SHIFTER3.2 (A1), LINE_RECEIVER3.3 (1Y), R87.2
ENC_PUL_OUT_A_HI_1: LINE_RECEIVER1.2 (1A), R31.1; also elsewhere on the board
ENC_PUL_OUT_A_HI_2: LINE_RECEIVER3.2 (1A), R35.1; also elsewhere on the board
ENC_PUL_OUT_A_LO_1: LINE_RECEIVER1.1 (1B), R31.2; also elsewhere on the board
ENC_PUL_OUT_A_LO_2: LINE_RECEIVER3.1 (1B), R35.2; also elsewhere on the board
ENC_PUL_OUT_B_GPIO_1: LEVEL_SHIFTER2.12 (B2); also elsewhere on the board
ENC_PUL_OUT_B_GPIO_1_5V: LEVEL_SHIFTER2.3 (A2), LINE_RECEIVER1.5 (2Y), R90.2
ENC_PUL_OUT_B_GPIO_2: LEVEL_SHIFTER3.12 (B2); also elsewhere on the board
ENC_PUL_OUT_B_GPIO_2_5V: LEVEL_SHIFTER3.3 (A2), LINE_RECEIVER3.5 (2Y), R86.2
ENC_PUL_OUT_B_HI_1: LINE_RECEIVER1.6 (2A), R32.2; also elsewhere on the board
ENC_PUL_OUT_B_HI_2: LINE_RECEIVER3.6 (2A), R36.2; also elsewhere on the board
ENC_PUL_OUT_B_LO_1: LINE_RECEIVER1.7 (2B), R32.1; also elsewhere on the board
ENC_PUL_OUT_B_LO_2: LINE_RECEIVER3.7 (2B), R36.1; also elsewhere on the board
ENC_PUL_OUT_C_GPIO_1: LEVEL_SHIFTER2.11 (B3); also elsewhere on the board
ENC_PUL_OUT_C_GPIO_1_5V: LEVEL_SHIFTER2.4 (A3), LINE_RECEIVER1.11 (3Y), R89.2
ENC_PUL_OUT_C_GPIO_2: LEVEL_SHIFTER3.11 (B3); also elsewhere on the board
ENC_PUL_OUT_C_GPIO_2_5V: LEVEL_SHIFTER3.4 (A3), LINE_RECEIVER3.11 (3Y), R85.2
ENC_PUL_OUT_C_HI_1: LINE_RECEIVER1.10 (3A), R34.2; also elsewhere on the board
ENC_PUL_OUT_C_HI_2: LINE_RECEIVER3.10 (3A), R38.2; also elsewhere on the board
ENC_PUL_OUT_C_LO_1: LINE_RECEIVER1.9 (3B), R34.1; also elsewhere on the board
ENC_PUL_OUT_C_LO_2: LINE_RECEIVER3.9 (3B), R38.1; also elsewhere on the board
GEN_PURPOSE_OUT_GPIO_A_1: LEVEL_SHIFTER1.13 (B1); also elsewhere on the board
GEN_PURPOSE_OUT_GPIO_A_1_5V: LEVEL_SHIFTER1.2 (A1), LINE_RECEIVER2.3 (1Y), R81.2
GEN_PURPOSE_OUT_GPIO_A_2: LEVEL_SHIFTER4.13 (B1); also elsewhere on the board
GEN_PURPOSE_OUT_GPIO_A_2_5V: LEVEL_SHIFTER4.2 (A1), LINE_RECEIVER4.3 (1Y), R84.2
GEN_PURPOSE_OUT_GPIO_B_1: LEVEL_SHIFTER1.12 (B2); also elsewhere on the board
GEN_PURPOSE_OUT_GPIO_B_1_5V: LEVEL_SHIFTER1.3 (A2), LINE_RECEIVER2.5 (2Y), R80.2
GEN_PURPOSE_OUT_GPIO_B_2: LEVEL_SHIFTER4.12 (B2); also elsewhere on the board
GEN_PURPOSE_OUT_GPIO_B_2_5V: LEVEL_SHIFTER4.3 (A2), LINE_RECEIVER4.5 (2Y), R83.2
GEN_PURPOSE_OUT_GPIO_C_1: LEVEL_SHIFTER1.11 (B3); also elsewhere on the board
GEN_PURPOSE_OUT_GPIO_C_1_5V: LEVEL_SHIFTER1.4 (A3), LINE_RECEIVER2.11 (3Y), R79.2
GEN_PURPOSE_OUT_GPIO_C_2: LEVEL_SHIFTER4.11 (B3); also elsewhere on the board
GEN_PURPOSE_OUT_GPIO_C_2_5V: LEVEL_SHIFTER4.4 (A3), LINE_RECEIVER4.11 (3Y), R82.2
GEN_PURPOSE_OUT_HI_A_1: LINE_RECEIVER2.2 (1A), R39.1; also elsewhere on the board
GEN_PURPOSE_OUT_HI_A_2: LINE_RECEIVER4.2 (1A), R51.1; also elsewhere on the board
GEN_PURPOSE_OUT_HI_B_1: LINE_RECEIVER2.6 (2A), R42.1; also elsewhere on the board
GEN_PURPOSE_OUT_HI_B_2: LINE_RECEIVER4.6 (2A), R54.1; also elsewhere on the board
GEN_PURPOSE_OUT_HI_C_1: LINE_RECEIVER2.10 (3A), R45.1; also elsewhere on the board
GEN_PURPOSE_OUT_HI_C_2: LINE_RECEIVER4.10 (3A), R57.1; also elsewhere on the board
GEN_PURPOSE_OUT_LO_A_1: C50.2, LINE_RECEIVER2.1 (1B), R40.1, R41.2; also elsewhere on the board
GEN_PURPOSE_OUT_LO_A_2: C55.2, LINE_RECEIVER4.1 (1B), R52.1, R53.2; also elsewhere on the board
GEN_PURPOSE_OUT_LO_B_1: C51.2, LINE_RECEIVER2.7 (2B), R43.1, R44.2; also elsewhere on the board
GEN_PURPOSE_OUT_LO_B_2: C56.2, LINE_RECEIVER4.7 (2B), R55.1, R56.2; also elsewhere on the board
GEN_PURPOSE_OUT_LO_C_1: C52.2, LINE_RECEIVER2.9 (3B), R46.1, R47.2; also elsewhere on the board
GEN_PURPOSE_OUT_LO_C_2: C57.2, LINE_RECEIVER4.9 (3B), R58.1, R59.2; also elsewhere on the board
unnamed: D7.C, OPTOCOUPLER.7 (ANODE4), R48.1
unnamed: D1.C, OPTOCOUPLER.1 (ANODE1), R17.1
unnamed: D2.C, OPTOCOUPLER.3 (ANODE2), R18.1
unnamed: D3.C, OPTOCOUPLER.5 (ANODE3), R27.1
unnamed: D4.C, OPTOCOUPLER2.1 (ANODE1), R28.1
unnamed: D5.C, OPTOCOUPLER2.3 (ANODE2), R29.1
unnamed: D6.C, OPTOCOUPLER2.5 (ANODE3), R30.1
SERVO_ALARM_AN_1: D7.A, OPTOCOUPLER.8 (CATHODE4); also elsewhere on the board
SERVO_ALARM_GPIO: OPTOCOUPLER.11 (V04), R49.1; also elsewhere on the board
S_GND: C47.1, C49.1, C50.1, C51.1, C52.1, C54.1, C55.1, C56.1, C57.1, C59.1, C60.1, C61.1, LEVEL_SHIFTER1.7 (GND), LEVEL_SHIFTER2.7 (GND), LEVEL_SHIFTER3.7 (GND), LEVEL_SHIFTER4.7 (GND), LINE_RECEIVER1.8 (GND), LINE_RECEIVER2.8 (GND), LINE_RECEIVER3.8 (GND), LINE_RECEIVER4.8 (GND), OPTOCOUPLER.9 (GND_2), OPTOCOUPLER.16 (GND), OPTOCOUPLER2.9 (GND_2), OPTOCOUPLER2.16 (GND), R41.1, R44.1, R47.1, R53.1, R56.1, R59.1, R79.1, R80.1, R81.1, R82.1, R83.1, R84.1, R85.1, R86.1, R87.1, R88.1, R89.1, R90.1, R91.1, R92.1; also elsewhere on the board
V_ON_5V_1: LINE_RECEIVER2.4 (1/2EN), LINE_RECEIVER2.12 (3/4EN); also elsewhere on the board
V_ON_5V_3: LINE_RECEIVER1.4 (1/2EN), LINE_RECEIVER1.12 (3/4EN); also elsewhere on the board
V_ON_5V_4: LINE_RECEIVER3.4 (1/2EN), LINE_RECEIVER3.12 (3/4EN); also elsewhere on the board
V_ON_5V_5: LINE_RECEIVER4.4 (1/2EN), LINE_RECEIVER4.12 (3/4EN); also elsewhere on the board

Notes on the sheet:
Line Receiver IC (Encoder Pulses)
OUTPUTS FROM SERVO
Photocoupler IC (Alarm Code Signals)
Line Receiver IC (General Purpose Output)
Level Shifter for Receiver ICs'

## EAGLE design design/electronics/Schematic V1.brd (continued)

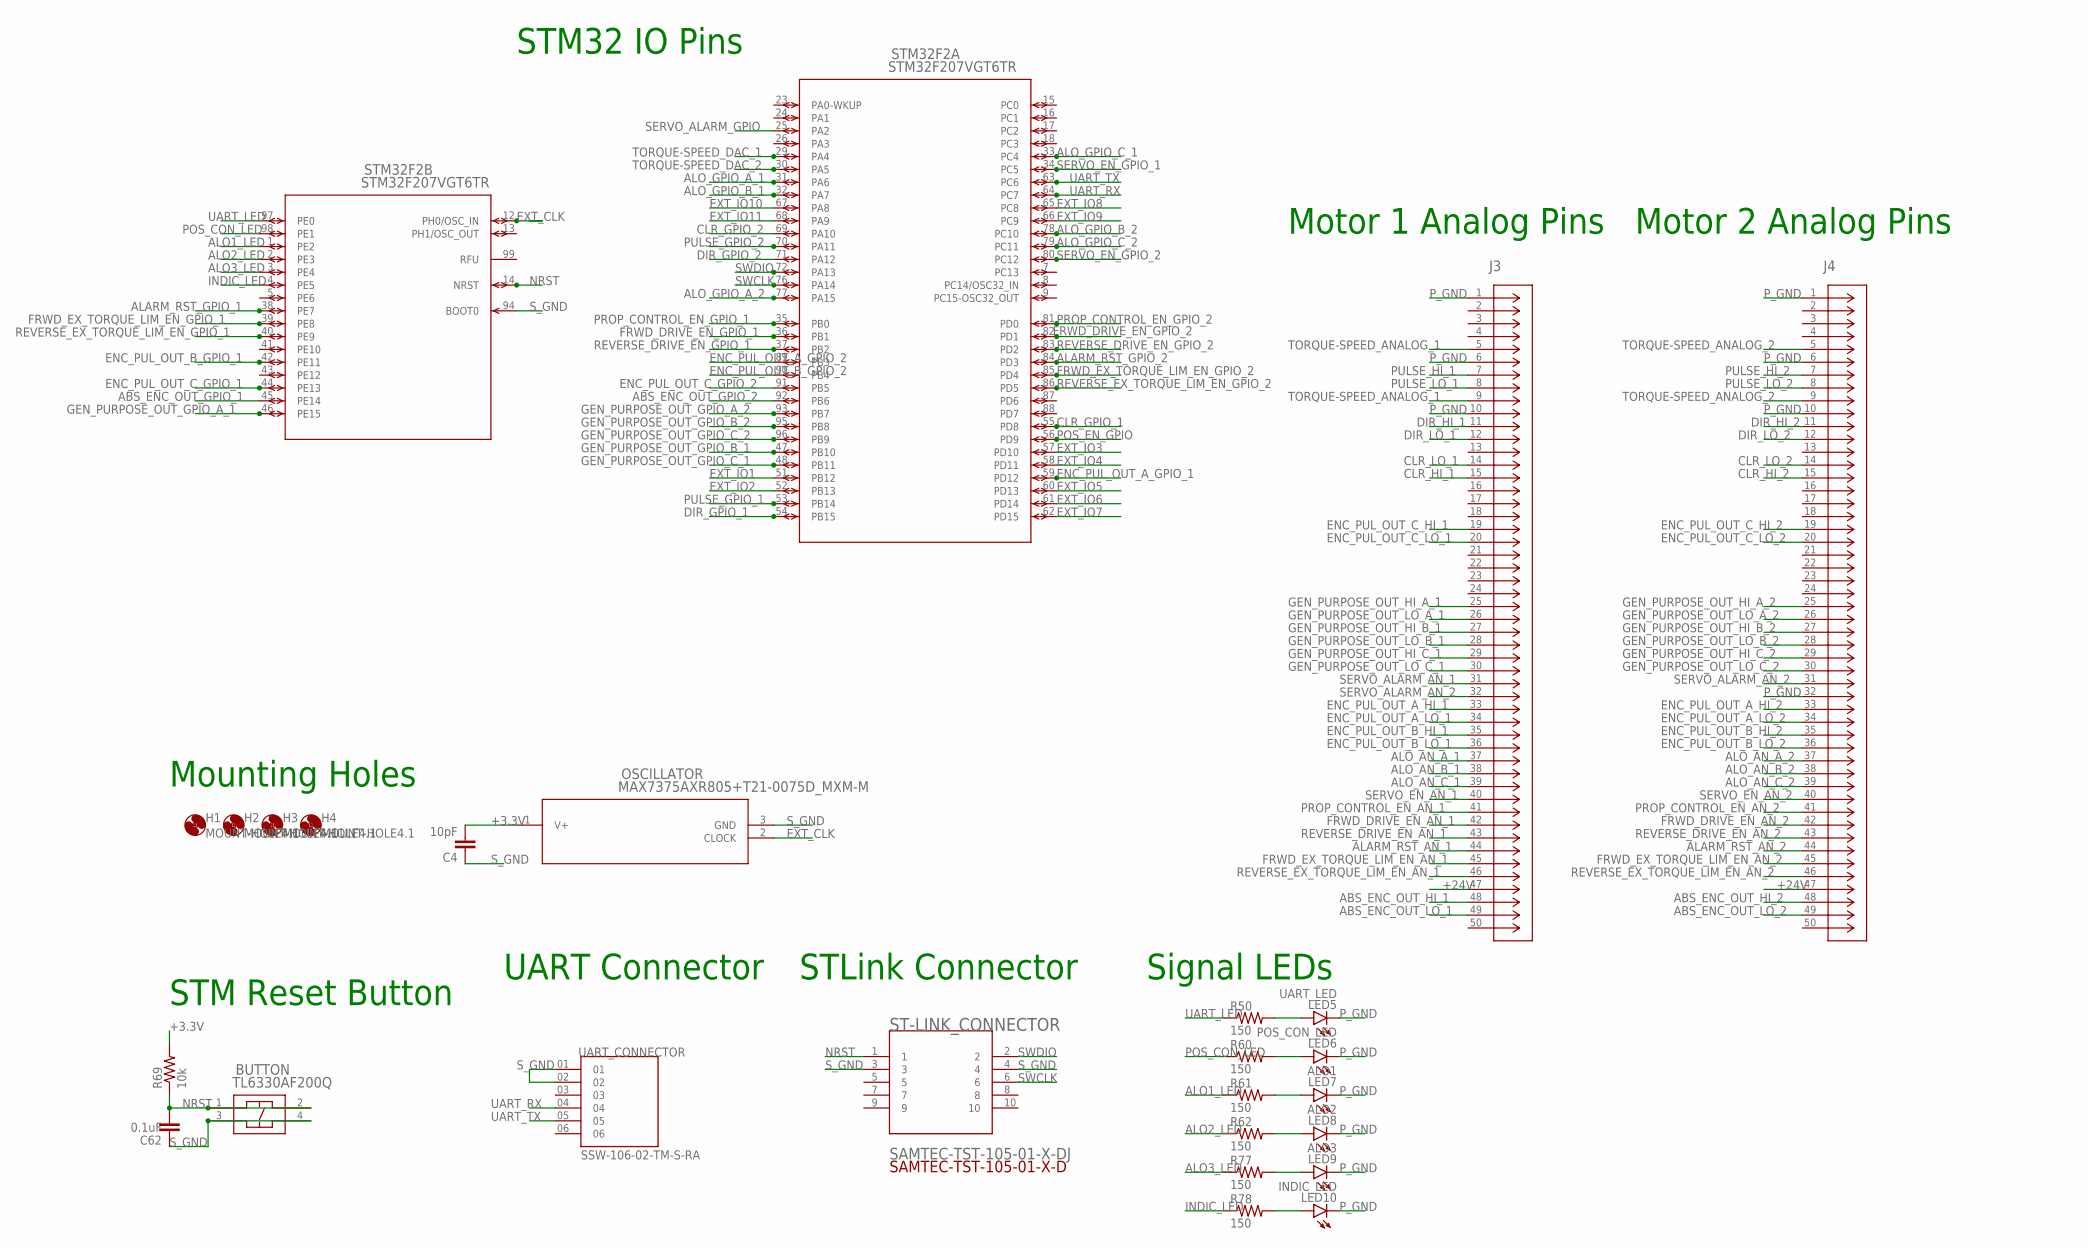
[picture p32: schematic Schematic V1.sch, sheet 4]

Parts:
BUTTON: TL6330AF200Q; TL6330_EWI
C4: 10pF; 0805
C62: 0.1uF; 0805
H1, H2, H3, H4: MOUNT-HOLE4.1; 4,1
J3, J4: DD50P564GTXLF; CONN_DD50P564GTXLF_AMP
LED5: UART_LED; CHIPLED_0805
LED6: POS_CON_LED; CHIPLED_0805
LED7: ALO1; CHIPLED_0805
LED8: ALO2; CHIPLED_0805
LED9: ALO3; CHIPLED_0805
LED10: INDIC_LED; CHIPLED_0805
OSCILLATOR: MAX7375AXR805+T21-0075D_MXM-M; 21-0075D_MXM-M
R50, R60, R61, R62, R77, R78: 150; R0805
R69: 10k; R0805
ST-LINK_CONNECTOR: SAMTEC-TST-105-01-X-DJ; SAMTEC-TST-105-01-X-D
STM32F2: STM32F207VGT6TR; LQFP100-14X14MM
UART_CONNECTOR: SSW-106-02-TM-S-RA; SAMTEC_SSW-106-02-TM-S-RA

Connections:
+3.3V: C4.2, OSCILLATOR.1 (V+), R69.2; also elsewhere on the board
+24V: J3.47, J4.47; also elsewhere on the board
ABS_ENC_OUT_GPIO_1: STM32F2.45 (PE14); also elsewhere on the board
ABS_ENC_OUT_GPIO_2: STM32F2.92 (PB6); also elsewhere on the board
ABS_ENC_OUT_HI_1: J3.48; also elsewhere on the board
ABS_ENC_OUT_HI_2: J4.48; also elsewhere on the board
ABS_ENC_OUT_LO_1: J3.49; also elsewhere on the board
ABS_ENC_OUT_LO_2: J4.49; also elsewhere on the board
ALARM_RST_AN_1: J3.44; also elsewhere on the board
ALARM_RST_AN_2: J4.44; also elsewhere on the board
ALARM_RST_GPIO_1: STM32F2.38 (PE7); also elsewhere on the board
ALARM_RST_GPIO_2: STM32F2.84 (PD3); also elsewhere on the board
ALO1_LED: R61.1, STM32F2.1 (PE2)
ALO2_LED: R62.1, STM32F2.2 (PE3)
ALO3_LED: R77.1, STM32F2.3 (PE4)
ALO_AN_A_1: J3.37; also elsewhere on the board
ALO_AN_A_2: J4.37; also elsewhere on the board
ALO_AN_B_1: J3.38; also elsewhere on the board
ALO_AN_B_2: J4.38; also elsewhere on the board
ALO_AN_C_1: J3.39; also elsewhere on the board
ALO_AN_C_2: J4.39; also elsewhere on the board
ALO_GPIO_A_1: STM32F2.31 (PA6); also elsewhere on the board
ALO_GPIO_A_2: STM32F2.77 (PA15); also elsewhere on the board
ALO_GPIO_B_1: STM32F2.32 (PA7); also elsewhere on the board
ALO_GPIO_B_2: STM32F2.78 (PC10); also elsewhere on the board
ALO_GPIO_C_1: STM32F2.33 (PC4); also elsewhere on the board
ALO_GPIO_C_2: STM32F2.79 (PC11); also elsewhere on the board
CLR_GPIO_1: STM32F2.55 (PD8); also elsewhere on the board
CLR_GPIO_2: STM32F2.69 (PA10); also elsewhere on the board
CLR_HI_1: J3.15; also elsewhere on the board
CLR_HI_2: J4.15; also elsewhere on the board
CLR_LO_1: J3.14; also elsewhere on the board
CLR_LO_2: J4.14; also elsewhere on the board
DIR_GPIO_1: STM32F2.54 (PB15); also elsewhere on the board
DIR_GPIO_2: STM32F2.71 (PA12); also elsewhere on the board
DIR_HI_1: J3.11; also elsewhere on the board
DIR_HI_2: J4.11; also elsewhere on the board
DIR_LO_1: J3.12; also elsewhere on the board
DIR_LO_2: J4.12; also elsewhere on the board
ENC_PUL_OUT_A_GPIO_1: STM32F2.59 (PD12); also elsewhere on the board
ENC_PUL_OUT_A_GPIO_2: STM32F2.89 (PB3); also elsewhere on the board
ENC_PUL_OUT_A_HI_1: J3.33; also elsewhere on the board
ENC_PUL_OUT_A_HI_2: J4.33; also elsewhere on the board
ENC_PUL_OUT_A_LO_1: J3.34; also elsewhere on the board
ENC_PUL_OUT_A_LO_2: J4.34; also elsewhere on the board
ENC_PUL_OUT_B_GPIO_1: STM32F2.42 (PE11); also elsewhere on the board
ENC_PUL_OUT_B_GPIO_2: STM32F2.90 (PB4); also elsewhere on the board
ENC_PUL_OUT_B_HI_1: J3.35; also elsewhere on the board
ENC_PUL_OUT_B_HI_2: J4.35; also elsewhere on the board
ENC_PUL_OUT_B_LO_1: J3.36; also elsewhere on the board
ENC_PUL_OUT_B_LO_2: J4.36; also elsewhere on the board
ENC_PUL_OUT_C_GPIO_1: STM32F2.44 (PE13); also elsewhere on the board
ENC_PUL_OUT_C_GPIO_2: STM32F2.91 (PB5); also elsewhere on the board
ENC_PUL_OUT_C_HI_1: J3.19; also elsewhere on the board
ENC_PUL_OUT_C_HI_2: J4.19; also elsewhere on the board
ENC_PUL_OUT_C_LO_1: J3.20; also elsewhere on the board
ENC_PUL_OUT_C_LO_2: J4.20; also elsewhere on the board
EXT_CLK: OSCILLATOR.2 (CLOCK), STM32F2.12 (PH0/OSC_IN)
EXT_IO1: STM32F2.51 (PB12)
EXT_IO2: STM32F2.52 (PB13)
EXT_IO3: STM32F2.57 (PD10)
EXT_IO4: STM32F2.58 (PD11)
EXT_IO5: STM32F2.60 (PD13)
EXT_IO6: STM32F2.61 (PD14)
EXT_IO7: STM32F2.62 (PD15)
EXT_IO8: STM32F2.65 (PC8)
EXT_IO9: STM32F2.66 (PC9)
EXT_IO10: STM32F2.67 (PA8)
EXT_IO11: STM32F2.68 (PA9)
FRWD_DRIVE_EN_AN_1: J3.42; also elsewhere on the board
FRWD_DRIVE_EN_AN_2: J4.42; also elsewhere on the board
FRWD_DRIVE_EN_GPIO_1: STM32F2.36 (PB1); also elsewhere on the board
FRWD_DRIVE_EN_GPIO_2: STM32F2.82 (PD1); also elsewhere on the board
FRWD_EX_TORQUE_LIM_EN_AN_1: J3.45; also elsewhere on the board
FRWD_EX_TORQUE_LIM_EN_AN_2: J4.45; also elsewhere on the board
FRWD_EX_TORQUE_LIM_EN_GPIO_1: STM32F2.39 (PE8); also elsewhere on the board
FRWD_EX_TORQUE_LIM_EN_GPIO_2: STM32F2.85 (PD4); also elsewhere on the board
GEN_PURPOSE_OUT_GPIO_A_1: STM32F2.46 (PE15); also elsewhere on the board
GEN_PURPOSE_OUT_GPIO_A_2: STM32F2.93 (PB7); also elsewhere on the board
GEN_PURPOSE_OUT_GPIO_B_1: STM32F2.47 (PB10); also elsewhere on the board
GEN_PURPOSE_OUT_GPIO_B_2: STM32F2.95 (PB8); also elsewhere on the board
GEN_PURPOSE_OUT_GPIO_C_1: STM32F2.48 (PB11); also elsewhere on the board
GEN_PURPOSE_OUT_GPIO_C_2: STM32F2.96 (PB9); also elsewhere on the board
GEN_PURPOSE_OUT_HI_A_1: J3.25; also elsewhere on the board
GEN_PURPOSE_OUT_HI_A_2: J4.25; also elsewhere on the board
GEN_PURPOSE_OUT_HI_B_1: J3.27; also elsewhere on the board
GEN_PURPOSE_OUT_HI_B_2: J4.27; also elsewhere on the board
GEN_PURPOSE_OUT_HI_C_1: J3.29; also elsewhere on the board
GEN_PURPOSE_OUT_HI_C_2: J4.29; also elsewhere on the board
GEN_PURPOSE_OUT_LO_A_1: J3.26; also elsewhere on the board
GEN_PURPOSE_OUT_LO_A_2: J4.26; also elsewhere on the board
GEN_PURPOSE_OUT_LO_B_1: J3.28; also elsewhere on the board
GEN_PURPOSE_OUT_LO_B_2: J4.28; also elsewhere on the board
GEN_PURPOSE_OUT_LO_C_1: J3.30; also elsewhere on the board
GEN_PURPOSE_OUT_LO_C_2: J4.30; also elsewhere on the board
INDIC_LED: R78.1, STM32F2.4 (PE5)
unnamed: LED5.A, R50.2
unnamed: LED6.A, R60.2
unnamed: LED7.A, R61.2
unnamed: LED8.A, R62.2
unnamed: LED9.A, R77.2
unnamed: LED10.A, R78.2
NRST: BUTTON.1, BUTTON.2, C62.2, R69.1, ST-LINK_CONNECTOR.1, STM32F2.14 (NRST)
POS_CON_LED: R60.1, STM32F2.98 (PE1)
POS_EN_GPIO: STM32F2.56 (PD9); also elsewhere on the board
PROP_CONTROL_EN_AN_1: J3.41; also elsewhere on the board
PROP_CONTROL_EN_AN_2: J4.41; also elsewhere on the board
PROP_CONTROL_EN_GPIO_1: STM32F2.35 (PB0); also elsewhere on the board
PROP_CONTROL_EN_GPIO_2: STM32F2.81 (PD0); also elsewhere on the board
PULSE_GPIO_1: STM32F2.53 (PB14); also elsewhere on the board
PULSE_GPIO_2: STM32F2.70 (PA11); also elsewhere on the board
PULSE_HI_1: J3.7; also elsewhere on the board
PULSE_HI_2: J4.7; also elsewhere on the board
PULSE_LO_1: J3.8; also elsewhere on the board
PULSE_LO_2: J4.8; also elsewhere on the board
P_GND: J3.1, J3.6, J3.10, J4.1, J4.6, J4.10, J4.32, LED5.C, LED6.C, LED7.C, LED8.C, LED9.C, LED10.C; also elsewhere on the board
REVERSE_DRIVE_EN_AN_1: J3.43; also elsewhere on the board
REVERSE_DRIVE_EN_AN_2: J4.43; also elsewhere on the board
REVERSE_DRIVE_EN_GPIO_1: STM32F2.37 (PB2); also elsewhere on the board
REVERSE_DRIVE_EN_GPIO_2: STM32F2.83 (PD2); also elsewhere on the board
REVERSE_EX_TORQUE_LIM_EN_AN_1: J3.46; also elsewhere on the board
REVERSE_EX_TORQUE_LIM_EN_AN_2: J4.46; also elsewhere on the board
REVERSE_EX_TORQUE_LIM_EN_GPIO_1: STM32F2.40 (PE9); also elsewhere on the board
REVERSE_EX_TORQUE_LIM_EN_GPIO_2: STM32F2.86 (PD5); also elsewhere on the board
SERVO_ALARM_AN_1: J3.31; also elsewhere on the board
SERVO_ALARM_AN_2: J3.32, J4.31
SERVO_ALARM_GPIO: STM32F2.25 (PA2); also elsewhere on the board
SERVO_EN_AN_1: J3.40; also elsewhere on the board
SERVO_EN_AN_2: J4.40; also elsewhere on the board
SERVO_EN_GPIO_1: STM32F2.34 (PC5); also elsewhere on the board
SERVO_EN_GPIO_2: STM32F2.80 (PC12); also elsewhere on the board
SWCLK: ST-LINK_CONNECTOR.6, STM32F2.76 (PA14)
SWDIO: ST-LINK_CONNECTOR.2, STM32F2.72 (PA13)
S_GND: BUTTON.3, BUTTON.4, C4.1, C62.1, OSCILLATOR.3 (GND), ST-LINK_CONNECTOR.3, ST-LINK_CONNECTOR.4, STM32F2.94 (BOOT0), UART_CONNECTOR.01, UART_CONNECTOR.02; also elsewhere on the board
TORQUE-SPEED_ANALOG_1: J3.5, J3.9; also elsewhere on the board
TORQUE-SPEED_ANALOG_2: J4.5, J4.9; also elsewhere on the board
TORQUE-SPEED_DAC_1: STM32F2.29 (PA4); also elsewhere on the board
TORQUE-SPEED_DAC_2: STM32F2.30 (PA5); also elsewhere on the board
UART_LED: R50.1, STM32F2.97 (PE0)
UART_RX: STM32F2.64 (PC7), UART_CONNECTOR.04
UART_TX: STM32F2.63 (PC6), UART_CONNECTOR.05

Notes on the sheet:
STM32 IO Pins
Motor 1 Analog Pins
STLink Connector
UART Connector
STM Reset Button
Motor 2 Analog Pins
Mounting Holes
Signal LEDs

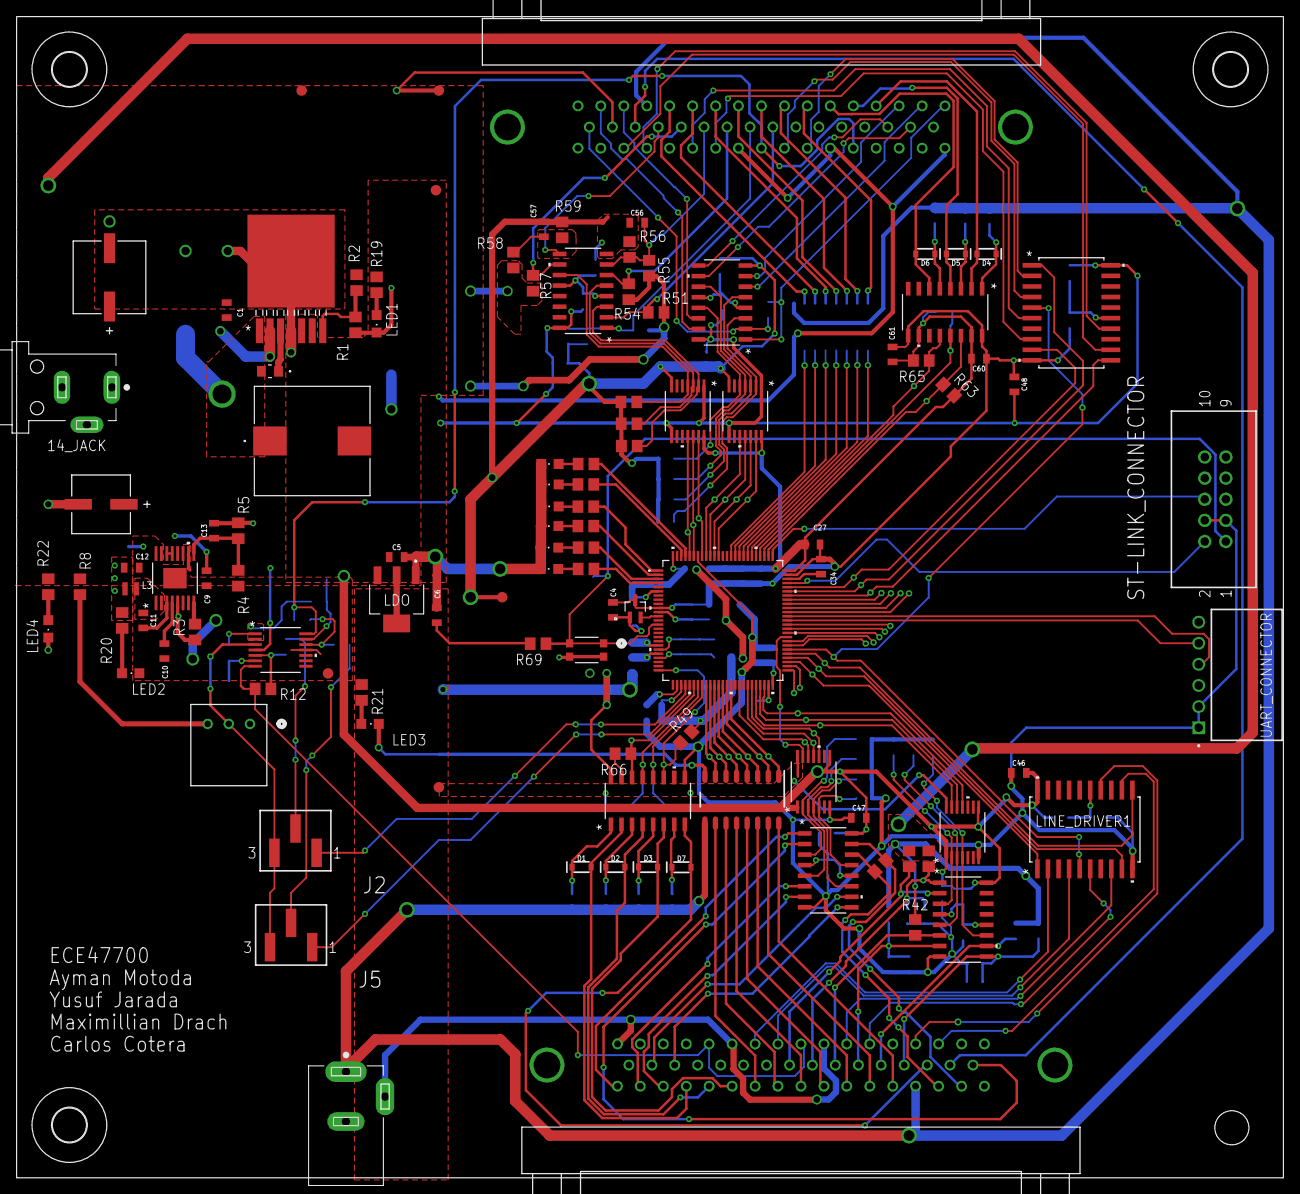
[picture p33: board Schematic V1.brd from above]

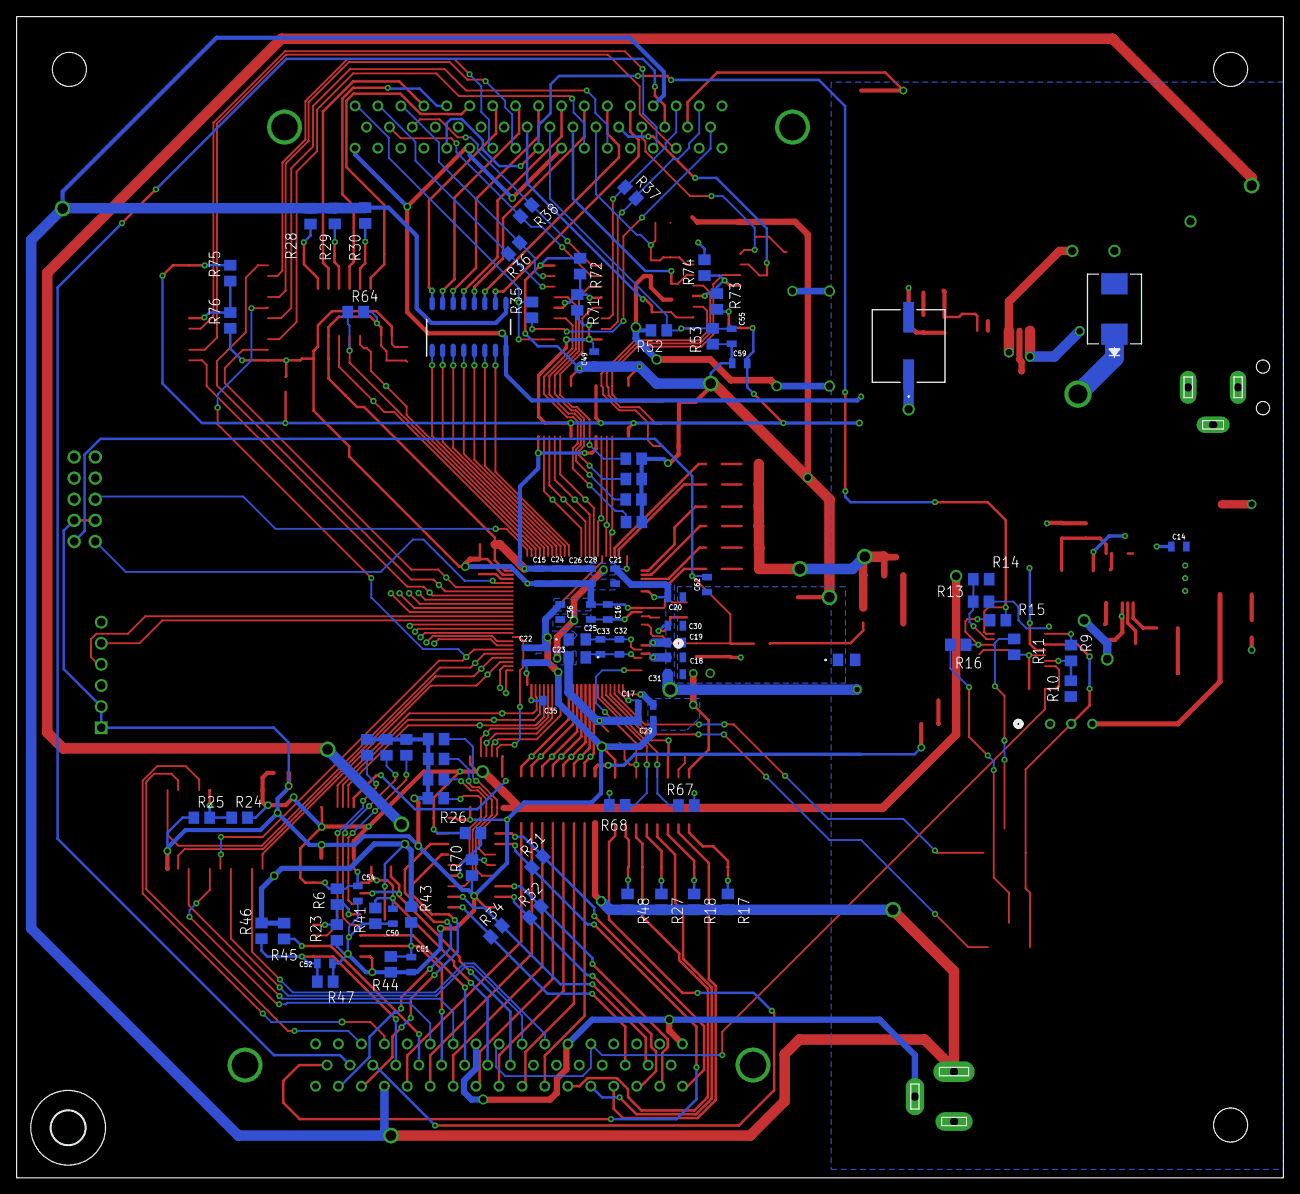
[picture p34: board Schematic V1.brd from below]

Board: 2 copper layers, 152.4 x 139.7 mm, 205 parts (91 on the bottom side), 185 nets.

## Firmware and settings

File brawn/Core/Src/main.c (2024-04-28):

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
/* Includes ------------------------------------------------------------------*/
#include "main.h"

/* USER CODE BEGIN Includes */
#include "stdio.h"
#include "string.h"
#include <stdlib.h>

/* USER CODE END Includes */

/* USER CODE BEGIN PTD */
#define MAX_Q_LEN 100
typedef struct {
  int xPul, yPul;
} Position;

typedef struct {
  Position moves[MAX_Q_LEN];
  unsigned char start;
  unsigned char end;
  unsigned char count;
} MoveQueue;

typedef enum State {
  IDLE = 'I',
  IN_GAME = 'S',
  RE_CENTER = 'R',
  DISCONNECTED = 'D'
} State;
/* USER CODE END PTD */

/* USER CODE BEGIN PM */
#define MAX_TX_LEN 30
#define TIMEOUT 1000
/* USER CODE END PM */

DAC_HandleTypeDef hdac;

RTC_HandleTypeDef hrtc;

TIM_HandleTypeDef htim1;
TIM_HandleTypeDef htim4;
TIM_HandleTypeDef htim12;

UART_HandleTypeDef huart6;

/* USER CODE BEGIN PV */
unsigned char c;
volatile unsigned char buffer[MAX_TX_LEN];
volatile int i = 0, msgReady = 0;
unsigned char msg[MAX_TX_LEN];
MoveQueue movQ = {0};
State gameState = DISCONNECTED;
#if defined(SIM) || defined(TRACK)
Position curPos = {0};
#endif
/* USER CODE END PV */

void SystemClock_Config(void);
static void MX_GPIO_Init(void);
static void MX_RTC_Init(void);
static void MX_TIM1_Init(void);
static void MX_TIM12_Init(void);
static void MX_DAC_Init(void);
static void MX_USART6_UART_Init(void);
static void MX_TIM4_Init(void);
/* USER CODE BEGIN PFP */
static void transmit(const char *);
//static void resetMotors(void);
static void sendPos(void);
static void handleCommand(const char);
static void enqueueMove(Position *);
static void handlePos(unsigned char *);
static int motorsReady(void);
static Position dequeueMove(void);
static void send_pulses(Position move);
static void alarm_reset(void);
/* USER CODE END PFP */

/**
  * @brief  The application entry point.
  * @retval int
  */
int main(void)
{
  /* MCU Configuration--------------------------------------------------------*/

  /* Reset of all peripherals, Initializes the Flash interface and the Systick. */
  HAL_Init();

  /* Configure the system clock */
  SystemClock_Config();

  /* Initialize all configured peripherals */
  MX_GPIO_Init();
  MX_RTC_Init();
  MX_TIM1_Init();
  MX_TIM12_Init();
  MX_DAC_Init();
  MX_USART6_UART_Init();
  MX_TIM4_Init();
  /* USER CODE BEGIN 2 */
  __HAL_UART_ENABLE_IT(&huart6, UART_IT_RXNE);
  HAL_UART_Receive_IT(&huart6, (unsigned char *)&c, 1);
  HAL_TIM_PWM_Start(&htim1, TIM_CHANNEL_4);
  HAL_TIM_PWM_Start(&htim12, TIM_CHANNEL_1);
  htim1.Instance->CNT = 0;
  htim12.Instance->CNT = 0;


  //Set the pin high to enable proportional control/action (make sure its set to zero for now)
  HAL_GPIO_WritePin(PROP_CONTROL_EN_GPIO_1_GPIO_Port, PROP_CONTROL_EN_GPIO_1_Pin, GPIO_PIN_RESET);
  HAL_GPIO_WritePin(PROP_CONTROL_EN_GPIO_2_GPIO_Port, PROP_CONTROL_EN_GPIO_2_Pin, GPIO_PIN_RESET);

  //Set the pin high to enable to enable forward direction movement
  HAL_GPIO_WritePin(FRWD_DRIVE_EN_GPIO_1_GPIO_Port, FRWD_DRIVE_EN_GPIO_1_Pin, GPIO_PIN_SET);
  HAL_GPIO_WritePin(FRWD_DRIVE_EN_GPIO_2_GPIO_Port, FRWD_DRIVE_EN_GPIO_2_Pin, GPIO_PIN_SET);
  //Set the pin high to enable to enable reverse direction movement
  HAL_GPIO_WritePin(REVERSE_DRIVE_EN_GPIO_1_GPIO_Port, REVERSE_DRIVE_EN_GPIO_1_Pin, GPIO_PIN_SET);
  HAL_GPIO_WritePin(REVERSE_DRIVE_EN_GPIO_2_GPIO_Port, REVERSE_DRIVE_EN_GPIO_2_Pin, GPIO_PIN_SET);

  //Enable high to limit the torque in the forward direction (set to zero for now)
  HAL_GPIO_WritePin(FRWD_EXT_TORQUE_LIM_EN_GPIO_1_GPIO_Port, FRWD_EXT_TORQUE_LIM_EN_GPIO_1_Pin, GPIO_PIN_RESET);
  HAL_GPIO_WritePin(FRWD_EXT_TORQUE_LIM_EN_GPIO_2_GPIO_Port, FRWD_EXT_TORQUE_LIM_EN_GPIO_2_Pin, GPIO_PIN_RESET);
  //Enable high to limit the torque in the reverse direction (set to zero for now)
  HAL_GPIO_WritePin(REVERSE_EXT_TORQUE_LIM_EN_GPIO_1_GPIO_Port, REVERSE_EXT_TORQUE_LIM_EN_GPIO_1_Pin, GPIO_PIN_RESET);
  HAL_GPIO_WritePin(REVERSE_EXT_TORQUE_LIM_EN_GPIO_2_GPIO_Port, REVERSE_EXT_TORQUE_LIM_EN_GPIO_2_Pin, GPIO_PIN_RESET);


  HAL_GPIO_WritePin(SERVO_EN_GPIO_1_GPIO_Port, SERVO_EN_GPIO_1_Pin, GPIO_PIN_RESET);
  HAL_GPIO_WritePin(SERVO_EN_GPIO_2_GPIO_Port, SERVO_EN_GPIO_2_Pin, GPIO_PIN_RESET);
//  HAL_GPIO_WritePin(SERVO_EN_GPIO_1_GPIO_Port, SERVO_EN_GPIO_1_Pin, GPIO_PIN_SET);
//  HAL_GPIO_WritePin(SERVO_EN_GPIO_2_GPIO_Port, SERVO_EN_GPIO_2_Pin, GPIO_PIN_SET);
//turns on motors
  /* USER CODE END 2 */

  /* Infinite loop */
  /* USER CODE BEGIN WHILE */
  int readyReported = 0;
  while (1)
  {
    /* USER CODE END WHILE */

    /* USER CODE BEGIN 3 */
    if (msgReady) {
#ifdef ECHO
      transmit((const char *)msg);
#else
      switch (msg[0]) {
      case '!':
        handleCommand(msg[1]);
        break;
      case 'X':
        handlePos(msg + 1);
        break;
      default:
        transmit("A999\0");
        gameState = DISCONNECTED;
      }
#endif
      msgReady = 0;
    }
#ifndef TRACK
    if (gameState == IN_GAME) {
      if (movQ.count) {
        if (motorsReady()) {
          readyReported = 0;
          send_pulses(dequeueMove());
        }
      }
//      else if (readyReported == 0 && motorsReady()) {
//        transmit("A555\0");
//        readyReported = 1;
//      }
    }



#endif
  }
  /* USER CODE END 3 */
}

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
/* USER CODE BEGIN 4 */


void HAL_GPIO_EXTI_Callback(uint16_t GPIO_Pin)
{
  /* Prevent unused argument(s) compilation warning */
  switch (GPIO_Pin) {
  case ALARM_NOTIF_Pin:
    HAL_GPIO_WritePin(GPIOA, ALO1_LED_A_Pin, HAL_GPIO_ReadPin(ALO_GPIO_A_1_GPIO_Port, ALO_GPIO_A_1_Pin));
    HAL_GPIO_WritePin(GPIOA, ALO2_LED_A_Pin, HAL_GPIO_ReadPin(ALO_GPIO_A_2_GPIO_Port, ALO_GPIO_A_2_Pin));
    HAL_GPIO_WritePin(GPIOB, ALO1_LED_B_Pin, HAL_GPIO_ReadPin(ALO_GPIO_B_1_GPIO_Port, ALO_GPIO_B_1_Pin));
    HAL_GPIO_WritePin(GPIOB, ALO2_LED_B_Pin, HAL_GPIO_ReadPin(ALO_GPIO_B_2_GPIO_Port, ALO_GPIO_B_2_Pin));
    HAL_GPIO_WritePin(GPIOC, ALO1_LED_C_Pin, HAL_GPIO_ReadPin(ALO_GPIO_C_1_GPIO_Port, ALO_GPIO_C_1_Pin));
    HAL_GPIO_WritePin(GPIOC, ALO2_LED_C_Pin, HAL_GPIO_ReadPin(ALO_GPIO_C_2_GPIO_Port, ALO_GPIO_C_2_Pin));
    alarm_reset();
  }
//  HAL_GPIO_ReadPin
}

void transmit(const char *m) {
  char s[MAX_TX_LEN];
  snprintf(s, sizeof(s), "%s#%s;\n", m, m);
  HAL_UART_Transmit(&huart6, (unsigned char *)s, strlen(s), HAL_MAX_DELAY);
}

//void resetMotors() { return; }

void handleCommand(const char code) {
  switch (code) {
  case 'R':
    gameState = RE_CENTER;
    transmit("!R\0");
    break;
  case 'I':
//    if (gameState == RE_CENTER || gameState == IN_GAME)
//      resetMotors();
    gameState = IDLE;
    //turns motors on
    HAL_GPIO_WritePin(SERVO_EN_GPIO_1_GPIO_Port, SERVO_EN_GPIO_1_Pin, GPIO_PIN_RESET);
    HAL_GPIO_WritePin(SERVO_EN_GPIO_2_GPIO_Port, SERVO_EN_GPIO_2_Pin, GPIO_PIN_RESET);
    transmit("!I\0");
    break;
  case 'D':
    gameState = DISCONNECTED;
    transmit("!D\0");
    HAL_GPIO_WritePin(SERVO_EN_GPIO_1_GPIO_Port, SERVO_EN_GPIO_1_Pin, GPIO_PIN_RESET);
    HAL_GPIO_WritePin(SERVO_EN_GPIO_2_GPIO_Port, SERVO_EN_GPIO_2_Pin, GPIO_PIN_RESET);
    break;
  case 'S':
    if (gameState != IDLE){
      HAL_GPIO_WritePin(SERVO_EN_GPIO_1_GPIO_Port, SERVO_EN_GPIO_1_Pin, GPIO_PIN_RESET);
      HAL_GPIO_WritePin(SERVO_EN_GPIO_2_GPIO_Port, SERVO_EN_GPIO_2_Pin, GPIO_PIN_RESET);
      transmit("A988\0");
    }
    else {
      gameState = IN_GAME;
      transmit("!S\0");
      //turn on motors
      HAL_GPIO_WritePin(SERVO_EN_GPIO_1_GPIO_Port, SERVO_EN_GPIO_1_Pin, GPIO_PIN_SET);
      HAL_GPIO_WritePin(SERVO_EN_GPIO_2_GPIO_Port, SERVO_EN_GPIO_2_Pin, GPIO_PIN_SET);
    }
    break;
  case '?':
    sendPos();
    break;
  default:
    transmit("A989\0");
  }
}

void enqueueMove(Position *m) {
  if (movQ.count++ == MAX_Q_LEN)
    transmit("A979\0");
  Position *end = &movQ.moves[movQ.end++];
  movQ.end %= MAX_Q_LEN;
  end->xPul = m->xPul;
  end->yPul = m->yPul;
}

void sendPos() {
#ifdef SIM
  char message[MAX_TX_LEN] = {0};
  sprintf(message, "X%d,%d", curPos.xPul, curPos.yPul);
  transmit(message);
#endif
}

void handlePos(unsigned char *data) {
  Position m;
  sscanf((char *)data, "%d,%d", &m.xPul, &m.yPul);
#ifdef TRACK
  curPos.xPul += m.xPul;
  curPos.yPul += m.yPul;
  sendPos();
#else
  enqueueMove(&m);
#endif
}

int motorsReady(void) {
#ifdef SIM
  return 1;
#else
//  return 1;
    return !HAL_GPIO_ReadPin(GPIOB, GEN_PURPOSE_OUT_GPIO_B_1_Pin) &&
        HAL_GPIO_ReadPin(GPIOA, GEN_PURPOSE_OUT_GPIO_A_1_Pin) && HAL_GPIO_ReadPin(GPIOA, GEN_PURPOSE_OUT_GPIO_A_2_Pin);
    // && HAL_GPIO_ReadPin(GPIOB, GEN_PURPOSE_OUT_GPIO_B_2_Pin);
#endif
}

Position dequeueMove() {
  if (!movQ.count--)
    transmit("A978\0");
  Position move = movQ.moves[movQ.start++];
  movQ.start %= MAX_Q_LEN;
  return move;
}

void send_pulses(Position move) {
#ifndef SIM
//  while (HAL_GPIO_ReadPin(GPIOC, GEN_PURPOSE_OUT_GPIO_C_1_Pin) || HAL_GPIO_ReadPin(GPIOC, GEN_PURPOSE_OUT_GPIO_C_2_Pin));
  HAL_GPIO_WritePin(GPIOB, GPIO_PIN_15, move.xPul < 0 ? GPIO_PIN_RESET : GPIO_PIN_SET);
  HAL_GPIO_WritePin(GPIOA, GPIO_PIN_12, move.yPul < 0 ? GPIO_PIN_RESET : GPIO_PIN_SET);
  uint16_t x_val = abs(move.xPul);
  uint16_t y_val = abs(move.yPul);
  int higher = x_val, lower = y_val;
  TIM_HandleTypeDef *higherTim = &htim12, *lowerTim = &htim1;

  if (lower > higher) {
    higher = y_val;
    lower = x_val;
    higherTim = &htim1;
    lowerTim = &htim12;
  }
  higher -= lower;
  while (lower--) {
    for (int i = 0; i < htim12.Instance->ARR; i++) {
      higherTim->Instance->CNT = i;
      lowerTim->Instance->CNT = i;
    }
  }
  lowerTim->Instance->CNT = 0;
  while (higher--) {
    for (int i = 0; i < htim12.Instance->ARR; i++) {
      higherTim->Instance->CNT = i;
    }
  }
  higherTim->Instance->CNT = 0;
  //function that waits for the motors to be ready and then sends a signbal when ready
  return;
#else
    curPos.xPul += move.xPul;
    curPos.yPul += move.yPul;
#endif
}

void HAL_UART_RxCpltCallback(UART_HandleTypeDef *huart) {
  switch (c) {
  case '#':
    msg[i] = buffer[i] = '\0';
    strcpy((char *)msg, (char *)buffer);
    i = 0;
    break;
  case ';':
    buffer[i] = '\0';
    i = 0;
    if (strcmp((char *)msg, (char *)buffer) || msgReady) {
      gameState = DISCONNECTED;
      msgReady = 0;
    }
    else
      msgReady = 1;
    break;
  default:
    buffer[i++] = c;
    if (i == MAX_TX_LEN)
      transmit("A969\0");
  }
}

void alarm_reset(void){
  //Enable high to reset the alarm codes on the motor, and then release.
  HAL_GPIO_WritePin(ALARM_RST_GPIO_1_GPIO_Port, ALARM_RST_GPIO_1_Pin, GPIO_PIN_SET);
  HAL_GPIO_WritePin(ALARM_RST_GPIO_2_GPIO_Port, ALARM_RST_GPIO_2_Pin, GPIO_PIN_SET);
  HAL_Delay(50);
  HAL_GPIO_WritePin(ALARM_RST_GPIO_1_GPIO_Port, ALARM_RST_GPIO_1_Pin, GPIO_PIN_RESET);
  HAL_GPIO_WritePin(ALARM_RST_GPIO_2_GPIO_Port, ALARM_RST_GPIO_2_Pin, GPIO_PIN_RESET);
}
/* USER CODE END 4 */
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


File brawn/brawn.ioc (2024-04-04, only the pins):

Mcu.UserName=STM32F207VGTx
PA10.GPIO_Label=CLR_GPIO_2
PA10.Signal=GPIO_Output
PA11.GPIO_Label=PULSE_GPIO_2
PA11.Signal=S_TIM1_CH4
PA12.GPIO_Label=DIR_GPIO_2
PA12.Signal=GPIO_Output
PA13.Signal=SYS_JTMS-SWDIO
PA14.Signal=SYS_JTCK-SWCLK
PA15.GPIO_Label=ALO_GPIO_A_2
PA15.Signal=GPIO_Input
PA2.GPIO_Label=ALARM_NOTIF
PA2.Signal=GPXTI2
PA4.Signal=COMP_DAC1_group
PA5.Signal=COMP_DAC2_group
PA6.GPIO_Label=ALO_GPIO_A_1
PA6.Signal=GPIO_Input
PA7.GPIO_Label=ALO_GPIO_B_1
PA7.Signal=GPIO_Input
PB0.GPIO_Label=PROP_CONTROL_EN_GPIO_1
PB0.Signal=GPIO_Output
PB1.GPIO_Label=FRWD_DRIVE_EN_GPIO_1
PB1.Signal=GPIO_Output
PB10.GPIO_Label=GEN_PURPOSE_OUT_GPIO_B_1
PB10.Signal=GPIO_Input
PB11.GPIO_Label=GEN_PURPOSE_OUT_GPIO_C_1
PB11.Signal=GPIO_Input
PB14.GPIO_Label=PULSE_GPIO_1
PB14.Signal=S_TIM12_CH1
PB15.GPIO_Label=DIR_GPIO_1
PB15.Signal=GPIO_Output
PB2.GPIO_Label=REVERSE_DRIVE_EN_GPIO_1
PB2.Signal=GPIO_Output
PB3.GPIO_Label=ENC_A_GPIO_2
PB3.Signal=GPIO_Input
PB4.GPIO_Label=ENC_B_GPIO_2
PB4.Signal=GPIO_Input
PB5.GPIO_Label=ENC_C_GPIO_2
PB5.Signal=GPIO_Input
PB6.GPIO_Label=ABS_ENC_GPIO_2
PB6.Signal=GPIO_Input
PB7.GPIO_Label=GEN_PURPOSE_OUT_GPIO_A_2
PB7.Signal=GPIO_Input
PB8.GPIO_Label=GEN_PURPOSE_OUT_GPIO_B_2
PB8.Signal=GPIO_Input
PB9.GPIO_Label=GEN_PURPOSE_OUT_GPIO_C_2
PB9.Signal=GPIO_Input
PC10.GPIO_Label=ALO_GPIO_B_2
PC10.Signal=GPIO_Input
PC11.GPIO_Label=ALO_GPIO_C_2
PC11.Signal=GPIO_Input
PC12.GPIO_Label=SERVO_EN_GPIO_2
PC12.Signal=GPIO_Output
PC4.GPIO_Label=ALO_GPIO_C_1
PC4.Signal=GPIO_Input
PC5.GPIO_Label=SERVO_EN_GPIO_1
PC5.Signal=GPIO_Output
PC6.Signal=USART6_TX
PC7.Signal=USART6_RX
PD0.GPIO_Label=PROP_CONTROL_EN_GPIO_2
PD0.Signal=GPIO_Output
PD1.GPIO_Label=FRWD_DRIVE_EN_GPIO_2
PD1.Signal=GPIO_Output
PD12.GPIO_Label=ENC_A_GPIO_1
PD12.Signal=GPIO_Input
PD2.GPIO_Label=REVERSE_DRIVE_EN_GPIO_2
PD2.Signal=GPIO_Output
PD3.GPIO_Label=ALARM_RST_GPIO_2
PD3.Signal=GPIO_Output
PD4.GPIO_Label=FRWD_EXT_TORQUE_LIM_EN_GPIO_2
PD4.Signal=GPIO_Output
PD5.GPIO_Label=REVERSE_EXT_TORQUE_LIM_EN_GPIO_2
PD5.Signal=GPIO_Output
PD8.GPIO_Label=CLR_GPIO_1
PD8.Signal=GPIO_Output
PD9.GPIO_Label=POS_EN_GPIO
PD9.Signal=GPIO_Output
PE0.GPIO_Label=ALO1_LED_A
PE0.Signal=GPIO_Output
PE1.GPIO_Label=ALO1_LED_B
PE1.Signal=GPIO_Output
PE11.GPIO_Label=ENC_B_GPIO_1
PE11.Signal=GPIO_Input
PE13.GPIO_Label=ENC_C_GPIO_1
PE13.Signal=GPIO_Input
PE14.GPIO_Label=ABS_ENC_GPIO_1
PE14.Signal=GPIO_Input
PE15.GPIO_Label=GEN_PURPOSE_OUT_GPIO_A_1
PE15.Signal=GPIO_Input
PE2.GPIO_Label=ALO1_LED_C
PE2.Signal=GPIO_Output
PE3.GPIO_Label=ALO2_LED_A
PE3.Signal=GPIO_Output
PE4.GPIO_Label=ALO2_LED_B
PE4.Signal=GPIO_Output
PE5.GPIO_Label=ALO2_LED_C
PE5.Signal=GPIO_Output
PE7.GPIO_Label=ALARM_RST_GPIO_1
PE7.Signal=GPIO_Output
PE8.GPIO_Label=FRWD_EXT_TORQUE_LIM_EN_GPIO_1
PE8.Signal=GPIO_Output
PE9.GPIO_Label=REVERSE_EXT_TORQUE_LIM_EN_GPIO_1
PE9.Signal=GPIO_Output
PH0-OSC_IN.Signal=RCC_OSC_IN
PH1-OSC_OUT.Signal=RCC_OSC_OUT

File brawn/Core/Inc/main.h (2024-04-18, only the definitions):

#define ALO1_LED_C_Pin GPIO_PIN_2
#define ALO1_LED_C_GPIO_Port GPIOE
#define ALO2_LED_A_Pin GPIO_PIN_3
#define ALO2_LED_A_GPIO_Port GPIOE
#define ALO2_LED_B_Pin GPIO_PIN_4
#define ALO2_LED_B_GPIO_Port GPIOE
#define ALO2_LED_C_Pin GPIO_PIN_5
#define ALO2_LED_C_GPIO_Port GPIOE
#define ALARM_NOTIF_Pin GPIO_PIN_2
#define ALARM_NOTIF_GPIO_Port GPIOA
#define ALARM_NOTIF_EXTI_IRQn EXTI2_IRQn
#define ALO_GPIO_A_1_Pin GPIO_PIN_6
#define ALO_GPIO_A_1_GPIO_Port GPIOA
#define ALO_GPIO_B_1_Pin GPIO_PIN_7
#define ALO_GPIO_B_1_GPIO_Port GPIOA
#define ALO_GPIO_C_1_Pin GPIO_PIN_4
#define ALO_GPIO_C_1_GPIO_Port GPIOC
#define SERVO_EN_GPIO_1_Pin GPIO_PIN_5
#define SERVO_EN_GPIO_1_GPIO_Port GPIOC
#define PROP_CONTROL_EN_GPIO_1_Pin GPIO_PIN_0
#define PROP_CONTROL_EN_GPIO_1_GPIO_Port GPIOB
#define FRWD_DRIVE_EN_GPIO_1_Pin GPIO_PIN_1
#define FRWD_DRIVE_EN_GPIO_1_GPIO_Port GPIOB
#define REVERSE_DRIVE_EN_GPIO_1_Pin GPIO_PIN_2
#define REVERSE_DRIVE_EN_GPIO_1_GPIO_Port GPIOB
#define ALARM_RST_GPIO_1_Pin GPIO_PIN_7
#define ALARM_RST_GPIO_1_GPIO_Port GPIOE
#define FRWD_EXT_TORQUE_LIM_EN_GPIO_1_Pin GPIO_PIN_8
#define FRWD_EXT_TORQUE_LIM_EN_GPIO_1_GPIO_Port GPIOE
#define REVERSE_EXT_TORQUE_LIM_EN_GPIO_1_Pin GPIO_PIN_9
#define REVERSE_EXT_TORQUE_LIM_EN_GPIO_1_GPIO_Port GPIOE
#define ENC_B_GPIO_1_Pin GPIO_PIN_11
#define ENC_B_GPIO_1_GPIO_Port GPIOE
#define ENC_C_GPIO_1_Pin GPIO_PIN_13
#define ENC_C_GPIO_1_GPIO_Port GPIOE
#define ABS_ENC_GPIO_1_Pin GPIO_PIN_14
#define ABS_ENC_GPIO_1_GPIO_Port GPIOE
#define GEN_PURPOSE_OUT_GPIO_A_1_Pin GPIO_PIN_15
#define GEN_PURPOSE_OUT_GPIO_A_1_GPIO_Port GPIOE
#define GEN_PURPOSE_OUT_GPIO_B_1_Pin GPIO_PIN_10
#define GEN_PURPOSE_OUT_GPIO_B_1_GPIO_Port GPIOB
#define GEN_PURPOSE_OUT_GPIO_C_1_Pin GPIO_PIN_11
#define GEN_PURPOSE_OUT_GPIO_C_1_GPIO_Port GPIOB
#define PULSE_GPIO_1_Pin GPIO_PIN_14
#define PULSE_GPIO_1_GPIO_Port GPIOB
#define DIR_GPIO_1_Pin GPIO_PIN_15
#define DIR_GPIO_1_GPIO_Port GPIOB
#define CLR_GPIO_1_Pin GPIO_PIN_8
#define CLR_GPIO_1_GPIO_Port GPIOD
#define POS_EN_GPIO_Pin GPIO_PIN_9
#define POS_EN_GPIO_GPIO_Port GPIOD
#define ENC_A_GPIO_1_Pin GPIO_PIN_12
#define ENC_A_GPIO_1_GPIO_Port GPIOD
#define CLR_GPIO_2_Pin GPIO_PIN_10
#define CLR_GPIO_2_GPIO_Port GPIOA
#define PULSE_GPIO_2_Pin GPIO_PIN_11
#define PULSE_GPIO_2_GPIO_Port GPIOA
#define DIR_GPIO_2_Pin GPIO_PIN_12
#define DIR_GPIO_2_GPIO_Port GPIOA
#define ALO_GPIO_A_2_Pin GPIO_PIN_15
#define ALO_GPIO_A_2_GPIO_Port GPIOA
#define ALO_GPIO_B_2_Pin GPIO_PIN_10
#define ALO_GPIO_B_2_GPIO_Port GPIOC
#define ALO_GPIO_C_2_Pin GPIO_PIN_11
#define ALO_GPIO_C_2_GPIO_Port GPIOC
#define SERVO_EN_GPIO_2_Pin GPIO_PIN_12
#define SERVO_EN_GPIO_2_GPIO_Port GPIOC
#define PROP_CONTROL_EN_GPIO_2_Pin GPIO_PIN_0
#define PROP_CONTROL_EN_GPIO_2_GPIO_Port GPIOD
#define FRWD_DRIVE_EN_GPIO_2_Pin GPIO_PIN_1
#define FRWD_DRIVE_EN_GPIO_2_GPIO_Port GPIOD
#define REVERSE_DRIVE_EN_GPIO_2_Pin GPIO_PIN_2
#define REVERSE_DRIVE_EN_GPIO_2_GPIO_Port GPIOD
#define ALARM_RST_GPIO_2_Pin GPIO_PIN_3
#define ALARM_RST_GPIO_2_GPIO_Port GPIOD
#define FRWD_EXT_TORQUE_LIM_EN_GPIO_2_Pin GPIO_PIN_4
#define FRWD_EXT_TORQUE_LIM_EN_GPIO_2_GPIO_Port GPIOD
#define REVERSE_EXT_TORQUE_LIM_EN_GPIO_2_Pin GPIO_PIN_5
#define REVERSE_EXT_TORQUE_LIM_EN_GPIO_2_GPIO_Port GPIOD
#define ENC_A_GPIO_2_Pin GPIO_PIN_3
#define ENC_A_GPIO_2_GPIO_Port GPIOB
#define ENC_B_GPIO_2_Pin GPIO_PIN_4
#define ENC_B_GPIO_2_GPIO_Port GPIOB
#define ENC_C_GPIO_2_Pin GPIO_PIN_5
#define ENC_C_GPIO_2_GPIO_Port GPIOB
#define ABS_ENC_GPIO_2_Pin GPIO_PIN_6
#define ABS_ENC_GPIO_2_GPIO_Port GPIOB
#define GEN_PURPOSE_OUT_GPIO_A_2_Pin GPIO_PIN_7
#define GEN_PURPOSE_OUT_GPIO_A_2_GPIO_Port GPIOB
#define GEN_PURPOSE_OUT_GPIO_B_2_Pin GPIO_PIN_8
#define GEN_PURPOSE_OUT_GPIO_B_2_GPIO_Port GPIOB
#define GEN_PURPOSE_OUT_GPIO_C_2_Pin GPIO_PIN_9
#define GEN_PURPOSE_OUT_GPIO_C_2_GPIO_Port GPIOB
#define ALO1_LED_A_Pin GPIO_PIN_0
#define ALO1_LED_A_GPIO_Port GPIOE
#define ALO1_LED_B_Pin GPIO_PIN_1
#define ALO1_LED_B_GPIO_Port GPIOE

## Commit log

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2024-01-14 Started working on CAD
    [Wheel_Consept.ipt]
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2024-01-16 Added CAD FILES AND EAGLE FILES
    [Assembly3.iam, AssemblyV1.0001.iam, AssemblyV1.iam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]
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2024-01-23 worked on STM Code
    [Assembly3.iam]
2024-01-24 Added BOM File & Updated Schematic
    [BOM.xlsx, Schematic V1.sch]
2024-01-25 STM COde
    [Assembly3.0001.iam]
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2024-02-01 Added A4 + Updated Schematic
    [BOM.xlsx, Schematic V1.sch]
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2024-02-06 CAD and STM CODE
    sorry for massive push
    [AKM2G-51DNCA_H.ipt, AKM2G-51DNCA_R.ipt, AKM2G-51X-ACDNCA00.0002.iam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]
2024-02-06 camera updates
    change bug in the avoidance where it was reading the x&y
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2024-02-08 finished up CAD
    [Final AssemblyV5.0001.iam, Final AssemblyV5.iam, FrontPlateV2.0003.ipt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]
2024-02-08 CAD ALMOST DONE
    [Final AssemblyV5.0001.iam, Final AssemblyV5.0003.iam, Final AssemblyV5.iam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]
2024-02-08 Updated Schematic with Main Features
    [BOM.xlsx, Schematic V1.sch]
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2024-02-10 fixed the constraint issue with assembly
    [Final AssemblyV5.0004.iam, Final AssemblyV5.0005.iam, Final AssemblyV5.iam]
2024-02-10 updated gitignore
    [Assembly3.0001.iam, Assembly3.iam, AssemblyV1.0001.iam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]
2024-02-10 re-structured repository
    [BOM.xlsx, Schematic V1.sch]
2024-02-11 Updated Schematic
    [BOM.xlsx, Schematic V1.sch]
2024-02-11 Updated Library and BOM
    [BOM.xlsx]
2024-02-11 Finished Schematics, Libraries, and BOM
    [BOM.xlsx, Schematic V1.sch]
2024-02-11 Updated BOM with Prices
    [BOM.xlsx]
2024-02-11 Created board layout, updated schematic on Buck Capacitors, Updated BOM, Updated Library
    [BOM.xlsx, Schematic V1.brd, Schematic V1.sch]
2024-02-12 updated website content
    [A7 - Bill of Materials.xlsx]
2024-02-12 removed website from repository
    [A7 - Bill of Materials.xlsx]
2024-02-13 new stm project and basic ui started
    [pyvenv.cfg]
2024-02-13 added parts
    [FrontPlateV2.0014.ipt, FrontPlateV2.0023.ipt, FrontPlateV2.ipt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]
2024-02-13 Bossed Up on the CAD
    [EndEffectorMotorAdapter.0011.ipt, EndEffectorMotorAdapter.ipt, Final AssemblyV5.0005.iam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]
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2024-02-14 Updated Schematic, board layout, BOM, and libraries
    [BOM.xlsx, Schematic V1.brd, Schematic V1.sch]
2024-02-14 Updated layout parts
    [BOM.xlsx, Schematic V1.brd, Schematic V1.sch]
2024-02-15 Updated Power Circuit Schematic + Layout + Components
    [BOM.xlsx, Schematic V1.brd, Schematic V1.sch]
2024-02-15 Updated Schematic and Board with a few components
    [BOM.xlsx, Schematic V1.brd, Schematic V1.sch]
2024-02-15 Updated BOM with updated part quantities
    [BOM.xlsx]
2024-02-16 Updated Power Scheme of STM32
    [Schematic V1.brd, Schematic V1.sch]
2024-02-16 Purchase Order Forms Added
    [Senior Design Purchase Request (Bearing).xlsx, Senior Design Purchase Request (DK).xlsx]
2024-02-17 Updated Schematic Layout
    [Schematic V1.brd]
2024-02-17 Updated Layout with most ICs on board now
    [Schematic V1.brd, Schematic V1.sch]
2024-02-18 More of the layout is added
    [Schematic V1.brd]
2024-02-20 Updated Layout with most traces
    [Schematic V1.brd]
2024-02-20 Moved UART signals to different pins for routing.
    [Schematic V1.brd, Schematic V1.sch]
2024-02-20 did one singular pin and im failing
2024-02-20 CAD progress
    [60_28 Ball.ipt, 60_28 Inner Ring.ipt, 60_28 Outer Ring.ipt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]
2024-02-21 Updated schematic, added amazon order purchase
    [Schematic V1.brd, Schematic V1.sch, Senior Design Purchase Request (Amazon).xlsx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]
2024-02-21 Updated Layout more
    [Schematic V1.brd, Schematic V1.sch]
2024-02-22 Layout almost done
    [Schematic V1.brd, Schematic V1.sch, Senior Design Purchase Request (Amazon).xlsx]
2024-02-23 Yay it's hooked up
    [Schematic V1.brd, Schematic V1.sch]
2024-02-26 Updated part library of barrel jack + stretched polygons
    [Schematic V1.brd, Schematic V1.sch]
2024-02-27 Updated PCB Connector Placement
    [Schematic V1.brd]
2024-02-27 Fixed traces
    [Schematic V1.brd]
2024-02-27 Updated Layout
    [Schematic V1.brd]
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2024-02-27 cad stuff
    [EndEffector.0011.ipt, EndEffector.dwg, EndEffector.ipt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]
2024-02-27 Finished PCB
    [Schematic V1.brd, Schematic V1.sch]
2024-02-28 Moved 2-frame page to separate page
    [Schematic V1.sch]
2024-02-28 Adding VIAs to STM traces
    [Schematic V1.brd]
2024-02-28 cad update
    [EndEffectorMotorAdapterV2.0001.ipt, EndEffectorMotorAdapterV2.0002.ipt, EndEffectorMotorAdapterV2.ipt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]
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2024-02-28 Updated Labels + Finished PCB
    [Schematic V1.brd, Schematic V1.sch]
2024-03-07 Added Traces
    [Schematic V1.brd, Schematic V1.sch]
2024-03-07 Added jumper connectors to DAC input, added EXT IO Pins
    [Schematic V1.brd, Schematic V1.sch]
2024-03-07 Finished Design
    [Schematic V1.brd, Schematic V1.sch]
2024-03-08 Added pull downs to level shifter 5V lines
    [Schematic V1.brd, Schematic V1.sch]
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2024-03-09 Updated silkscreen and trace error
    [Schematic V1.brd]
2024-03-09 Fixed Silkscreen cover over EXT_GPIO Pins
    [Schematic V1.brd]
2024-03-25 Added file ignoring and developped sentry.py
    [pyvenv.cfg]
2024-03-26 Created an abstract message.py class. Safely implements the string manipulation logic for messages transmitted over UART
2024-03-27 added stm32 actuation package
    The stm config is correct here
    [main.c, main.h]
2024-03-29 de-bugged first draft main.c on school computer
    -Carlos
    [main.c, main.h]
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2024-04-01 Testing protocol.py.
    Sync command test passing, other commands failing.
    [connection.py, main.c, message.py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]
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2024-04-01 Redesigned protocol.py, cleaned stm code.
    [connection.py, main.c, protocol.py]
2024-04-02 Cleared repo to reorganize with poetry and git commands.
    [60_28 Ball.ipt, 60_28 Inner Ring.ipt, 60_28 Outer Ring.ipt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]
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2024-04-02 Uploaded documentation.
    [60_28 Ball.ipt, 60_28 Inner Ring.ipt, 60_28 Outer Ring.ipt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]
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2024-04-08 Partially de-bugged UI and game
    Started integration tests between Pathfinder and Game. This commit is decent enough to allow Max to commence proper testing and improvements of the pathfinder class
    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
    [connection.py, protocol.py]
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2024-04-11 Fixed Tkinter concurrency issue where timer was blocking UI.
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2024-04-18 game state changes,
    fixed threading issues, also some issues with one punch detection
    [connection.py, protocol.py]
2024-04-28 all mechincal designs
    [1000TVL v6.step, BUSHING.ipt, EndEffector.0011.ipt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]

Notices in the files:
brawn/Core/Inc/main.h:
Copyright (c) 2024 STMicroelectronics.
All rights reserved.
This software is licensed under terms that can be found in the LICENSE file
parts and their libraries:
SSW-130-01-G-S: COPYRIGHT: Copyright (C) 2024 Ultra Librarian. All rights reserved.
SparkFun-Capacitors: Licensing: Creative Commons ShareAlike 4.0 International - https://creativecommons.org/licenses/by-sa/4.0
